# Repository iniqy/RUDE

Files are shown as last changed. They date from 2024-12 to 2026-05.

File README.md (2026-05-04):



# Robak Unstoppable Dream Edition

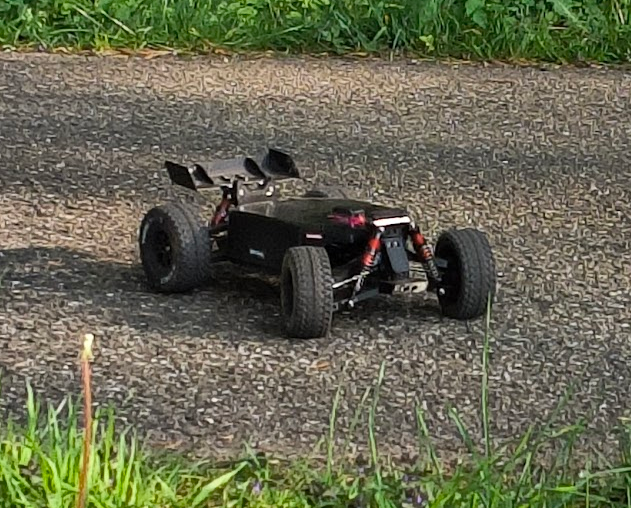
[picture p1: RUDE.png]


Join the Discord (https://discord.gg/Cc8tsbZAE3)

An open-source 3D Printed RC car. RUDE **v1.0** was a heavily modified version of [Robak v2.2](https://github.com/robaki-dev/robak/).

The most resilient RC car on the planet! More driving and less repairing. This car only stops when your battery is empty. If you break this car after flying out of your apartment window I failed.

[Bill of Materials and Printing Instructions](https://docs.google.com/spreadsheets/d/1WngvrndMor4qRpjjS1Nden6RAWPPBa2J9SWaNV3pnVo/edit?usp=sharing)

[Assembly Guide](https://docs.google.com/presentation/d/1uc42ykA9YBD8isIoi1eW3QIydnOAwHwjOqGhsE2rHdI/edit?usp=sharing)

## 4th of May 2026 v2.0 RELEASE
V2.0 has superior handling due to direct steering (see last v1.1 review below). It also offers a superior drivetrain with the optional center differential. In addition it has newly designed front arms that remove play in front wheel alignment and make installation of smaller wheels possible. Motorplates have more space for pinion gears. The chassis can be printed in two pieces so most printers should be able to print RUDE v2.0.

### FAQ: What is this car going to cost me?

Complete hardware kit without plastic parts: Low budget: €200. Premium: €400. The BOM lists all premium parts. Compared to similar-spec commercial RC vehicles, RUDE is half the price.

Also maintenance cost is much lower, since a commercial crown gear costs around €30 to replace. Meanwhile RUDE complete differential incl. crown gear, spider gears and more cost only €4.

### FAQ: Is this car child friendly?

No, this toy is an absolute weapon.

## v1.1 reviews

> "10/10"

> "this car is freakin awesome"

> "Super fun project"

> "I just could not bring myself to buy him a crappy off the shelf RC car for Christmas. So he got a RUDE"

> "Just can’t stop driving it!"

> "it is a beast"

> "behaves like a jelly bear"

Join discord for more...

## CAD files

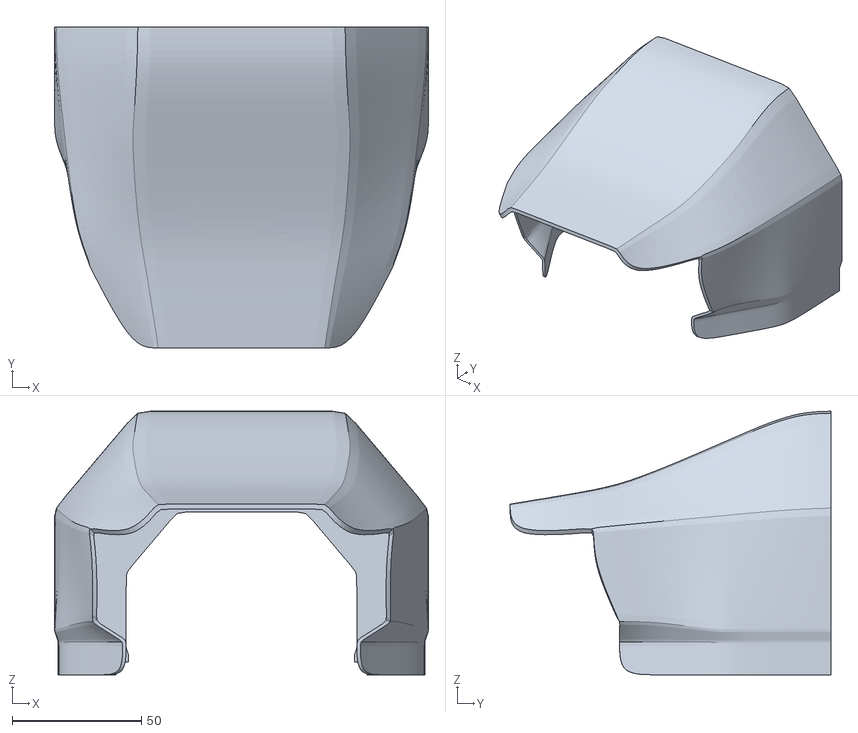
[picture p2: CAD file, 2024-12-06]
ROBAK_STL/BodyF.stl
144.8 x 124.1 x 102.0

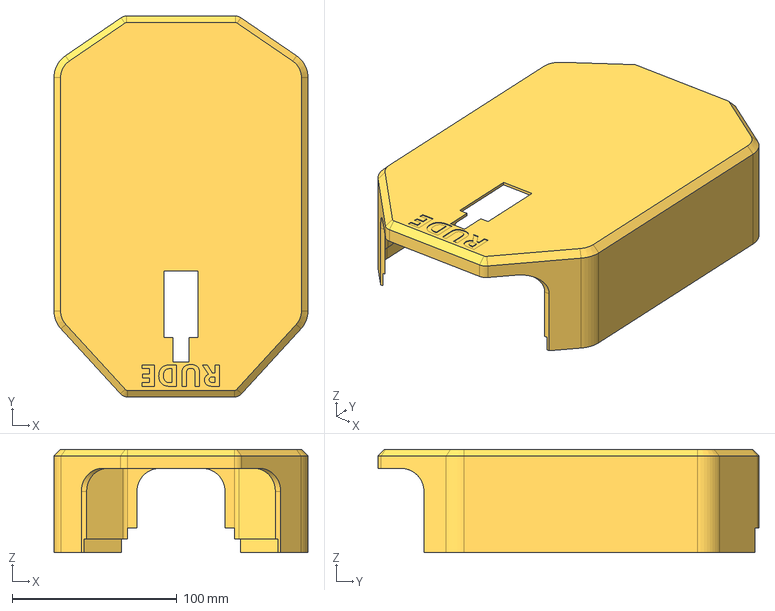
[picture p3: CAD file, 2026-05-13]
STEP/Body.step
154.4 x 231.6 x 62.8 mm

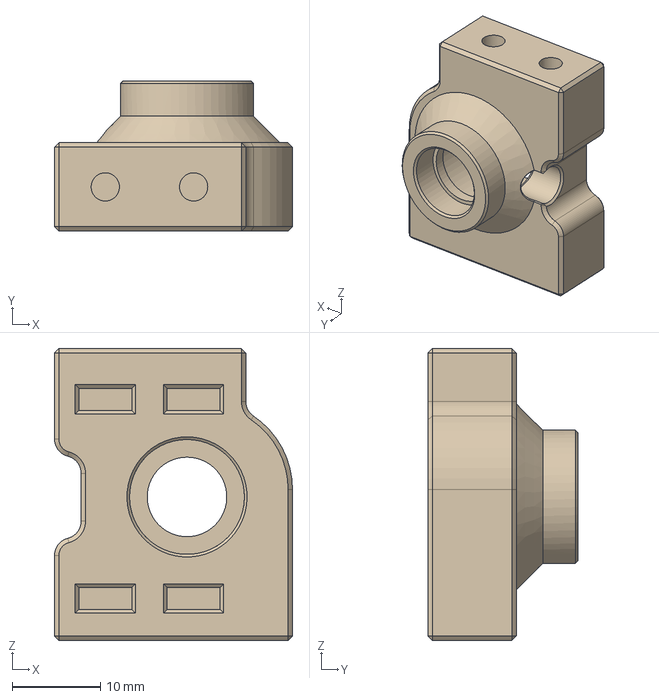
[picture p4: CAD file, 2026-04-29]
STEP/CD/10760/CenterDiffPlate-TRX_10760.step
26.9 x 17.0 x 33.1 mm

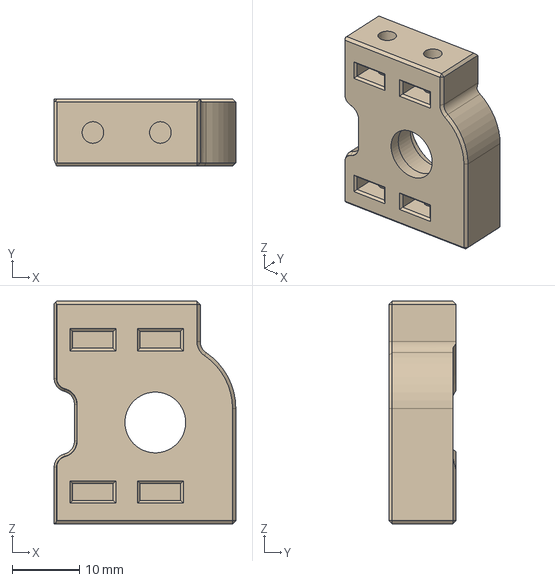
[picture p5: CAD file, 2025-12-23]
STEP/CD/Normal/CenterDiffPlate.step
26.9 x 10.0 x 33.1 mm

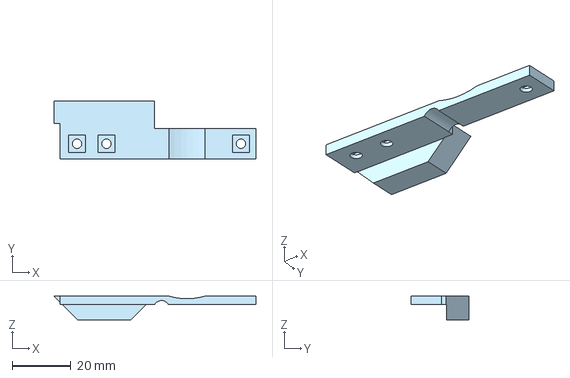
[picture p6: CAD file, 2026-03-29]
STEP/CD/Rear Insert.step
68.7 x 19.6 x 8.13 mm

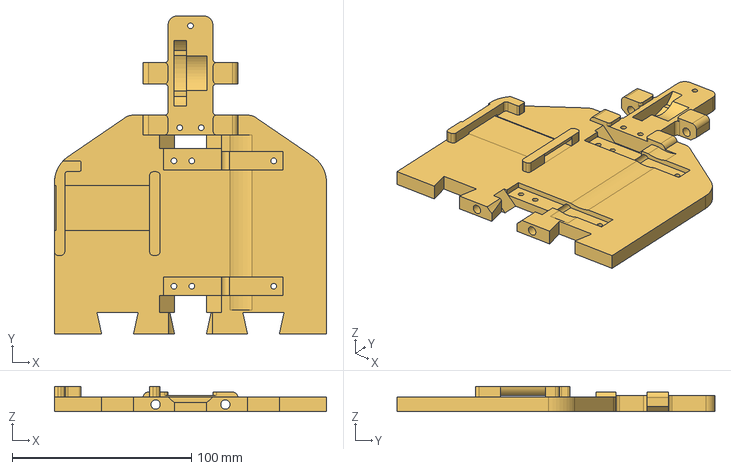
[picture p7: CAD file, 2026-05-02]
STEP/Chassis/Chassis Rear.step
152.0 x 177.7 x 14.2 mm

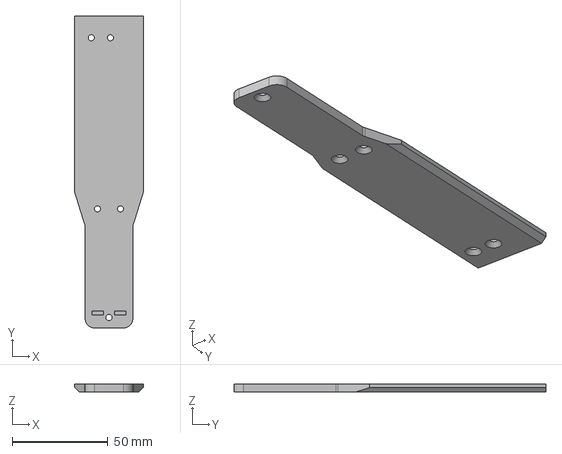
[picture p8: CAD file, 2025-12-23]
STEP/EXPERIMENTAL/Skid_plate_front.step
36.0 x 163.4 x 4.00 mm

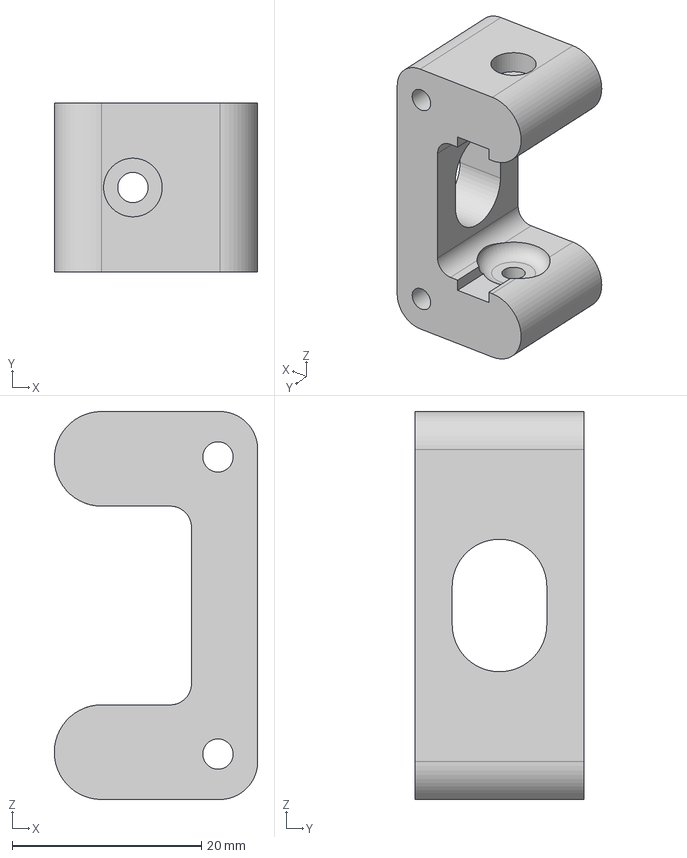
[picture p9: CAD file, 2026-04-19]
STEP/Front arms/2x_CarrierHubF.step
21.5 x 17.9 x 41.0 mm

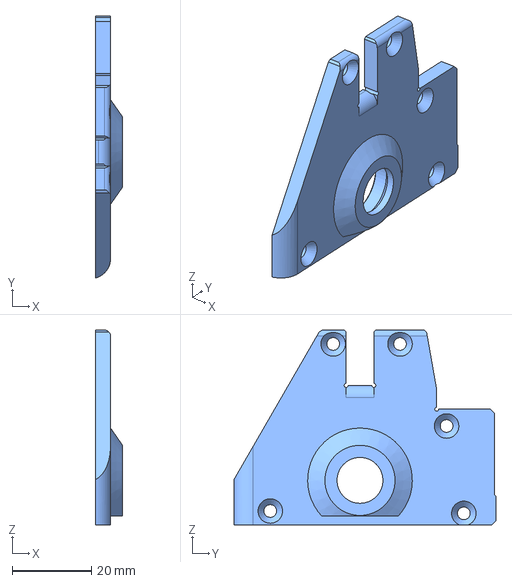
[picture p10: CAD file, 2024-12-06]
STEP/FrontAndRearDiffCase/DiffCaseHeadSide.step
6.90 x 66.3 x 49.3 mm

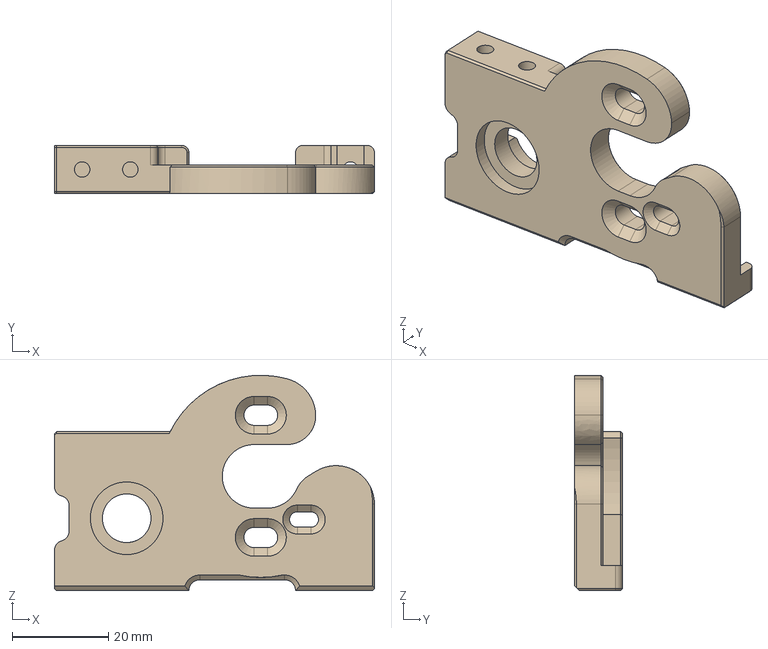
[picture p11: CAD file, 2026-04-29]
STEP/Motorplates/CD/MotorPlate_MAX8_CD.step
66.5 x 10.0 x 44.8 mm

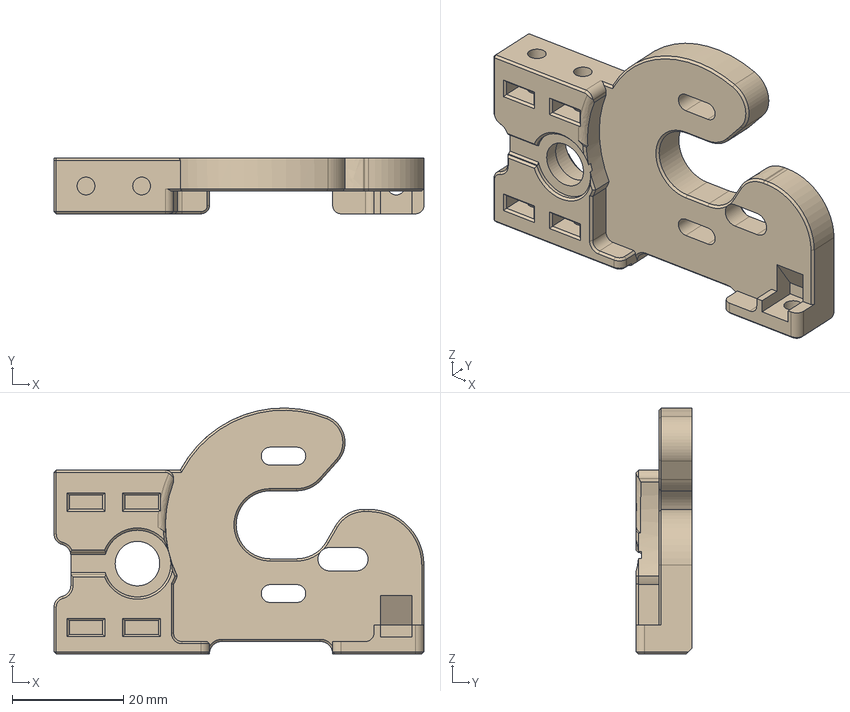
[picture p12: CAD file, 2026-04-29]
STEP/Motorplates/Non-CD/MotorPlate_Ysido.step
66.5 x 10.0 x 44.2 mm

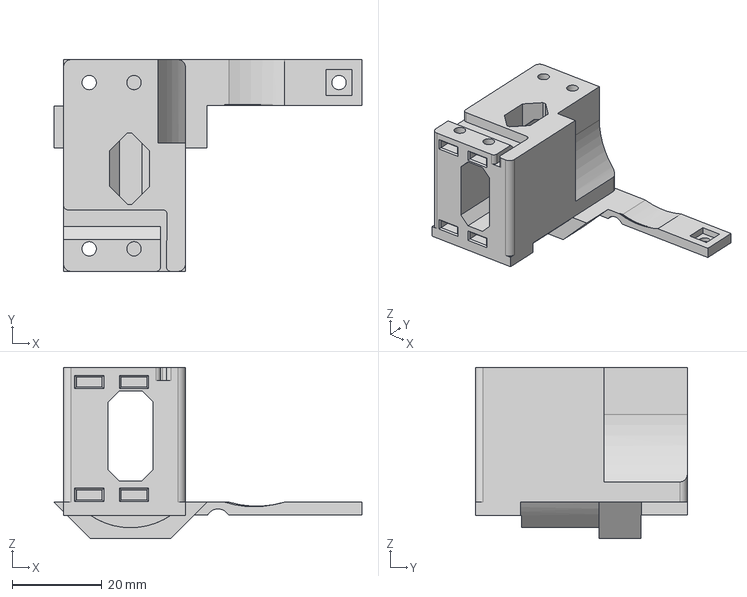
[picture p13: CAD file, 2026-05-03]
STEP/No-CD/Center Insert.step
68.7 x 47.2 x 38.2 mm

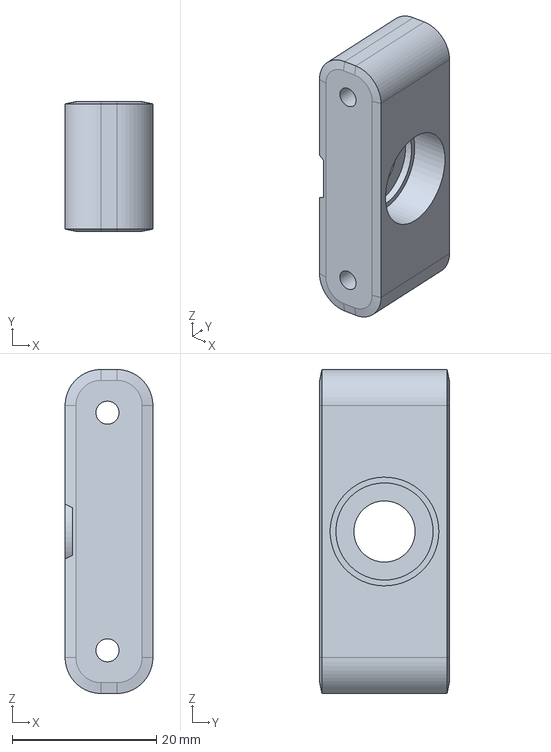
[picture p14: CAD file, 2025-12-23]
STEP/Rear arms/2x_CarrierHubR.step
12.2 x 18.0 x 45.0 mm

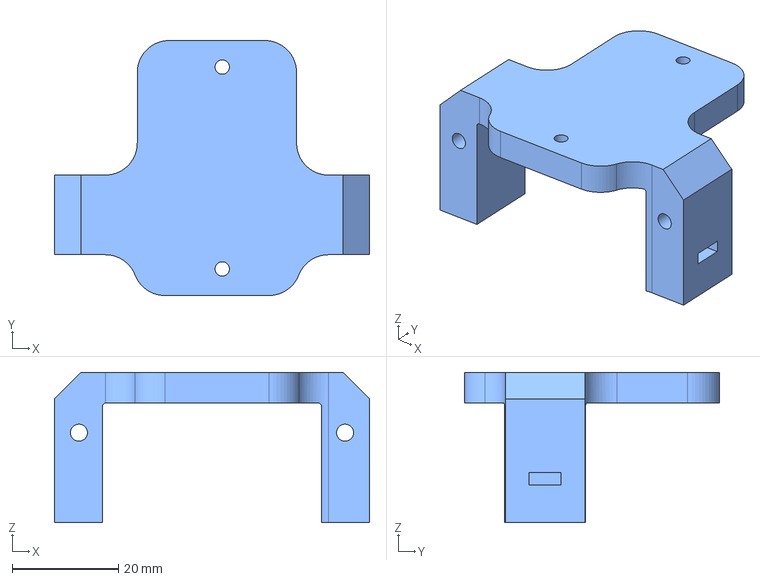
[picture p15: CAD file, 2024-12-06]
STEP/ServoMounts/Ezrun MAX10/ServoMount_EZRUN_MAX10.step
59.3 x 48.0 x 28.3 mm

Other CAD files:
STEP/Motorplates/CD/TRX_10760/MotorPlate_Quicrun_42_CD_10760.step
STEP/ServoMounts/Generic_1to10/ServoMount.step
STEP/ServoMounts/Generic_1to8/ServoMount_bigESC.step
STEP/ServoMounts/Quicrun 8BL150/ServoMount_Quicrun8BL150.step
Outdated/HSP02016_insert.stl
Outdated/v1.0/BellCrankL.step
Outdated/v1.0/BellCrankR.step
Outdated/v1.0/BodyF_Clip.step
Outdated/v1.0/Braces/KNOG/Brace_KNOG.step
Outdated/v1.0/Braces/KNOG/LEDClip_KNOG.stl
Outdated/v1.0/Braces/Stock/Brace.step
Outdated/v1.0/Chassis.step
Outdated/v1.0/Chassis_longmotor_70-82mm.step
Outdated/v1.0/DiffCaseCentralPart.step
Outdated/v1.0/Motorplates/MotorPlate_36mm.step
Outdated/v1.0/Motorplates/MotorPlate_42mm_MAX8.step
Outdated/v1.0/Motorplates/MotorPlate_42mm_ysido.step
Outdated/v1.0/Motorplates/MotorPlate_blank.step
Outdated/v1.0/Outdated/BodyR_Clip.step
Outdated/v1.0/TopDeckF.step
Outdated/v1.0/TopDeckR.step
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

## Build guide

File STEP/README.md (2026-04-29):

CD = Center Differential
No-CD = No Center Differential

Choose 1.

All the others are needed except Wing.

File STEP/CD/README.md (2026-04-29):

Choose:
Normal = DIY (Do It Yourself) center differential (made from metal HSP 02024 as in assembly guide CD part 1)
Or:
Traxxas 10760 center differential

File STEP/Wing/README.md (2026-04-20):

Designed by @ambrmart

https://www.printables.com/model/1690925-bodies-and-wings-for-the-robak-2-rc-car

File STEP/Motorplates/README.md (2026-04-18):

Print one for your motor that fits your setup (Center Differential or No CD)

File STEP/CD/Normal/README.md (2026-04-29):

# DIY Center Diff option

## BOM

* 4x M3x8 countersunk hex screws
* 4x M3 square nuts (DIN 562, not the thicker ones)
* 1x HSP 02024 diff. If you have spares parts of one, the crown gear and 1-2 diff cups are not needed
* 2 HSP 02030 (to use in the diff conversion)
* 4-5mm of steel tubing (OD 5mm, 0.2mm wall thickness)

## Printing guidance

Print in stiff materials. ASA/PC/PC-CF are good choices for motor plates. 

Regarding the gear mount, ASA is a good choice for gear mount. Avoid PC does not work as it cracks easily and seems to react to silicone oil, PA-GF/CF may also be a good alternative (needs further testing).

Gear mount needs supports in the center.

## Assembly instructions

### 1. Center diff conversion

* Print the corresponding adapter depending on the spur gear revision
1. Disassemble the diff, on the crown gear side, remove spider gear from diff cup.
2. Cut 4-5mm of steel tubing, grab a HSP 02030 shaft and place the steel tubing on the thinner end. Install the spider gear there. It should look like this (TODO: insert picture here)
3. Place the rubber washer in the pocket of the printed adapter.
4. Install the shaft - don’t forget the metal washer!
5. If using shafts for both ends of the diff, repeat steps 3 through 6 on the other end. Otherwise, proceed to next step.
6. Fill with diff oil and close the diff with the printed adapter. Make sure diff case fits in the groove and screws are as tight as possible. Don’t forget loctite if using metal diff case.
7. Place the square nuts on the adapter. Grab the spur gear and secure it with 4 M3 8mm countersunk screws.

### 2. Center diff installation

1. Install center diff on motor plate (using bearing).
2. Place another bearing on the center diff plate, place center diff in the middle.
3. Install the above subassembly on chassis. Tuning note: Center diff should spin without binding but not loose, i.e. similar rotation as with rear/front diffs. Use shims as needed.
4. Install cup on motor plate side shaft.
5. Install motor on motor plate, do the gear mesh at this time.

### 3. Tuning

1. Tuning step - at this time, give the motor a spin for ~10-15 seconds. Everything should roll smoothly, if anything binds or diff gets hot, stop and check diff rolls smoothly without the motor.
2. Check that Diff is not leaking any diff oil. If it does, stop and verify screws from step 1.f are screwed to the very end and that diff case is correctly seated on the adapter.
3. Set up the rear diff part of the car as you would the front one, i.e. using the shorter 02030.
4. Assemble the rest of the car using normal procedure, repeating motor test after finished installing front and rear diffs.

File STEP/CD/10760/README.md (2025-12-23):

# Non-DIY option

## Introduction

Currently 2 options are supported:

- Traxxas 10760
- Traxxas 6878 with 50T spur gear. This is actually a slipper clutch, not a center differential. This is a cheaper option vs the center differential, but requires more frequent tuning.

Note that with either of these options, the spur gears are mod 0.8, not 0.6. You will need to switch pinion gears accordingly.

It should be possible to use adjustable shafts for both front and rear axles, however using adjustable shafts in the rear axle will impact the minimum teeth

### 1. Center diff installation

Instructions here will be the same for slipper clutch, instructions for the center differential are as follows:

1. Install center diff / slipper clutch on motor plate (using bearing).
2. Place another bearing on the center diff plate, place center diff in the middle.
3. Install the above subassembly on chassis. Tuning note: Center diff should spin without binding but not loose, i.e. similar rotation as with rear/front diffs. Use shims as needed.
4. Install motor on motor plate, do the gear mesh at this time.

### 2. Tuning steps

1. At this time, give the motor a spin for ~10-15 seconds. Everything should roll smoothly, if anything binds or diff gets hot, stop and check diff rolls smoothly without the motor.
2. Set up the rear diff part of the car as you would the front one, i.e. using the shorter 02030.
3. Assemble the rest of the car using normal procedure, repeating motor test after finished installing front and rear diffs.
4. If using slipper clutch, you will need to properly adjust it depending on your driving session (looser for grass, tighter for on road), as well as periodically (slipper clutch has pads that are expected to wear out over time)

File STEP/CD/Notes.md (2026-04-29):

# Center Differential

# Introduction

There are 3 options for center differential support:

* (cheapest) DIY solution based on the HSP 02024 differential, replacing the crown differential with the standard spur gear, with a 3D printable gear mount.
* (most expensive) Traxxas 10760 (or 10760X)
* (intermediate cost) Traxxas 6878. Note that this is a slipper clutch, not a center differential.

# Expectations

1. Note that with a center diff the driving experience changes a bit - in particular there is the possibility of overpowering the diff if applying full throttle from stand still (which can also be problematic on a non-center diff configuration as it stresses the drivetrain). Tinkering with oil viscosity may allow for different driving styles. For bashing, 500K-1M CST is recommended, but further testing is recommended.
2. A commercial diff will likely be more reliable than the DIY option but they tend to be significantly more expensive. Gear Mount being plastic will cause the seal effectiveness to vary depending on several factors. Over-diffing a lot may cause the diff to become very hot, which can cause the mount to degrade. Using a material with higher heat deflection is recommended.
3. Due to gear clearance, battery is supposed to be placed vertically, which limits the maximum capacity.

# BOM

These are in addition to the base BOM (common accross all 3 options):

* 2x 10x15x4 bearings
* 2x M3x12 screws (all screws are hex countersunk head screws - DIN7991)
* 2x M3x16 screws
* 2 dogbone shafts (sizes depend on configuration but 1x63mm, rear, 1x77mm front at this time), or
* Adjustable shafts - 65-75mm (2)
* Thicker diff oil - 500-2M CST is recommended
* 4x M3 square nuts (DIN 562, these can be thicker as the center diff plate is actually a heavily modded motor plate)
* 1 HSP 02030 (to be used in the rear diff)

DIY Center Diff requires additional hardware, please look at the corresponding document.

Things being reused:

* Spur gear
* Motor plate bearing, screws, square nuts
* Everything else aside from the printed parts

# Future developments

- Potential alternatives may be considered (particularly a CNC version for the gear mount) to further improve reliability.
- Additional options for center differentials would be considered. However, there are a few factors that limit possibilities. Limiting factors:
* 42mm is the current maximum for gear diameter. Bigger gears run the risk of sitting too close to the battery.
* Moving the axle center can cause clearance problems with the servo mount.

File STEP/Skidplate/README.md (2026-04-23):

Choose:
Front + Rear (mainly for small beds)
Or:
One Piece

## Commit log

2024-08-11 v1.1 experimental release
    [BellCrankL.step, BellCrankR.step, Body.step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]
2024-08-13 fixed steering link hole
    [Chassis.step, Chassis_longmotor.step]
2024-09-05 v1.1 topdeck update
    more space for motor
    [TopDeck.step]
2024-11-22 docs update
    [ServoMount_Quicrun8BL150.step, hsp02024_diff_shim.step]
2024-11-22 RUDE diffs (and body update)
    [BodyF.stl, BodyR.stl, BodyR_Clip.step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]
2024-11-22 stiff filament section update
2024-11-22 Servomount ezrun MAX10 update
    [ServoMount_EZRUN_MAX10.step]
2024-11-22 bom update
2024-11-22 added more links to BOM
2024-11-22 updated BOM links
2024-11-22 v1.1 update
    [BellCrankL.step, BellCrankR.step, Body.step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]
2024-12-06 RUDE v1.1
    [ArmFL.step, ArmFR.step, ArmRL.step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]
2024-12-19 Added filament section to BOM
2025-01-06 Added HSP diff cups to spares in BOM
2025-01-09 Updated bearing links
2025-01-09 Ceramic bearings link
2025-02-04 ysido + topdeck upgrade + remove short motor variants
    [Chassis.step, Chassis_longmotor.step, MotorPlate_YSIDO.step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]
2025-02-06 Thicker topdecks + body fix + better motorplates
    [Body.step, MotorPlate_MAX10.step, MotorPlate_blank.step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]
2025-03-16 MAX10 motorplate, 8BL150 ESC mount, 350mm rods brace updates
    [Brace.step, MotorPlate_MAX10.step, ServoMount_Quicrun8BL150.step]
2025-03-16 8BL150 fix + rods link + titanium bolts
    [ServoMount_Quicrun8BL150.step]
2025-03-23 Steering link + towers :D + body
    [Link.step, LowProfileBody.step, SteeringLink.step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]
2025-03-23 Fix towers + stronger tallbody
    [TallBody.step, Tower.step, Tower_beast.step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]
2025-04-04 Steering link fix
    [SteeringLink.step]
2025-09-27 - Minor tweaks to Race Body (should be final now).
    [Race Body.stl]
2025-10-21 - Re-did center insert to fix several bugs.
    [Center Insert.step]
2025-12-06 - Redesign of Center Insert. - Fixed clearance issue with Race Body (thanks to Furial!).
    [Center Insert.step, Race Body.stl]
2025-12-23 Update BOM.md
    Added Center Diff section BOM
2025-12-23 Update BOM.md
    Classic configuration BOM
2025-12-23 Update DIY center diff README.md
    Updated material instructions to avoid PC for the gear mount.
2025-12-23 Update BOM.md
    Added a couple of clarifications, typo fix.
2025-12-23 Update BOM.md
    Correction regarding Traxxas 10760R.
2025-12-23 RUDE v2.0 (untested)
    [Chassis.step, Chassis_front.step, Chassis_rear.step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]
2026-03-29 v2.0 update
    [ArmFL.step, ArmFR.step, ArmRL.step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]
2026-03-30 velcro mounts
    [Body.step, TopDeck.step]
2026-04-05 Updated body + topdeck velcro indicators
    [Body.step, TopDeck.step]
2026-04-13 Update motorplates and wing
    [CenterDiffPlate.step, MotorPlate_MAX10.step, MotorPlate_MAX8.step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]
2026-04-18 Enhanced motorplates + CD motorplates
    [2x_CarrierHubF.step, 2x_CarrierHubR.step, Center Insert.step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]
2026-04-19 Motorplates + Front arms update
    [2x_CarrierHubF.step, Front arms - ArmFL.step, Front arms - ArmFR.step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]
2026-04-20 Topdeck height increased for servo saver drive shaft clearance
    [Body.step, TopDeck.step, WingMountStud.step]
2026-04-20 Added missing velcro indicators
    [TopDeck.step]
2026-04-21 Small bearing hole added to CD motorplates
    [MotorPlate_MAX10_CD.step, MotorPlate_MAX8_CD.step, MotorPlate_Quicrun_42_CD.step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]
2026-04-21 Bearing tolerance added + FHCS for 1/8 motor mounts
    [MotorPlate_MAX10_CD.step, MotorPlate_MAX8.step, MotorPlate_MAX8_CD.step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]
2026-04-22 Motorplate fixes + optional one piece chassis
    [CenterDiffPlate No Diff Cup.step, CenterDiffPlate.step, Chassis_front.step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]
2026-04-23 One piece skid plate added + aesthetics improved
    [Chassis Front.step, Chassis One Piece.step, Chassis Rear.step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]
2026-04-29 Topdeck update + TRX 10760 CD support
    [Body.step, Calibration.stl, Center Insert.step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]
2026-05-02 Tweaks + TRX 10760 compatibility fixes
    [Body.step, Chassis Front.step, Chassis One Piece.step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]
2026-05-03 - Center insert changes:
    * Removed motor chamfer and aligned with top deck instead.
    * Enlarged spur gear insert feature to match updated chassis.
    [Center Insert.step]
2026-05-05 ServohornMount added
    [ServohornMount.step]
2026-05-13 Body fix
    [Body.step]

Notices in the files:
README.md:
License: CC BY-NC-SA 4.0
